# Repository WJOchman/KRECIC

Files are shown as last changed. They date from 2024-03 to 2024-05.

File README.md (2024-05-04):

# KRECIC (Knowledge and Robotics Educational Companion for Interactive Computing) | A Modular Wheeled Robot for Educational Usage
## ELEE1036 Individual Project at the University of Greenwich | Academic Year 2023/24

<p align="center">
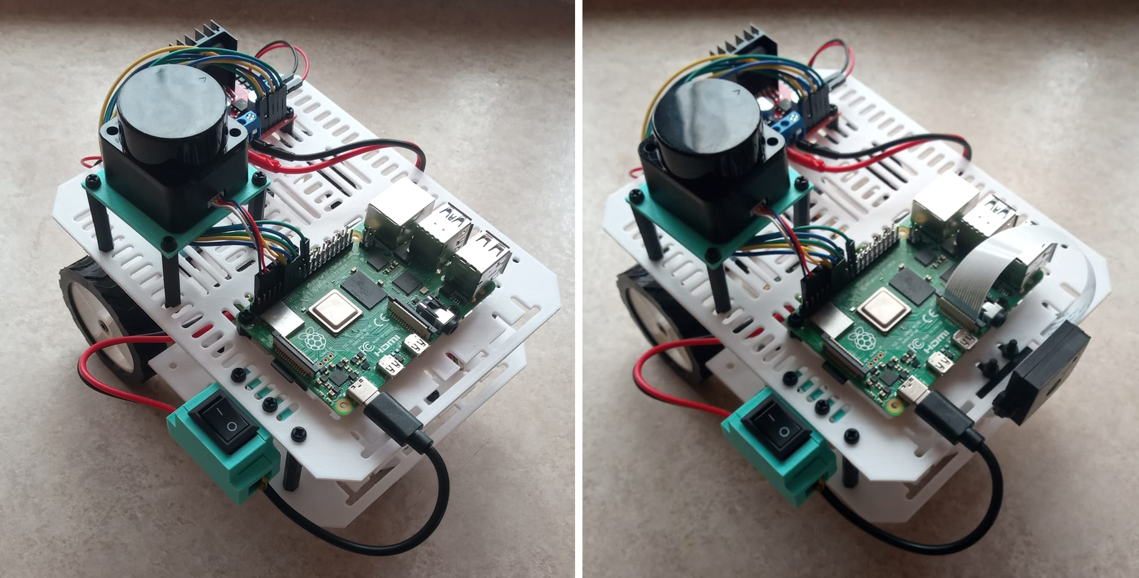
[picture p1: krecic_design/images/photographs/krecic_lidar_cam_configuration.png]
krecic_image
  
</p>

## Table of Contents
- [Introduction](#introduction)
- [Hardware Setup](#hardware-setup)
  - [Components](#components)
  - [Manufacturing](#manufacturing)
  - [Assembly](#assembly)
- [Software Setup](#software-setup)
  - [Operating System](#operating-system)
  - [Robot Operating System](#robot-operating-system)
  - [Motor and Movement Control](#motor-and-movement-control)
  - [Camera Module](#camera-module)
  - [LiDAR Module](#lidar-module)
- [Contributors](#contributors)
- [License](#license) 

## Introduction
This project has been developed as a final year project for the BEng in Computer Engineering (Hons) at the University of Greenwich (Academic Year 2023/24). 

This project can only be used for educational purposes and it cannot be used for commercial purposes. All credits must be given to the creator and the University of Greenwich. 

This document presents an overview of both the hardware and software setups to successfully re-create this project. This repository is organised into two predominant sections: (a) hardware and (b) software.

## Hardware Setup
This sections outlines the necessary steps in successfully setting up KRECIC's hardware components. 

Keep in mind, that KRECIC has been designed with modularity and evolution in mind. Therefore, the exact components are not necessary. 

### Components
Consider the [Bill of Materials (BOM)](/krecic_design/electronics/KRECIC_BOM.pdf) of all electronics you may need to get started with the building of KRECIC.

### Manufacturing 
To successfully manufacture the 3D printable components found [here](/krecic_design/stl_files/), you will require either an FDM or resin printer. The following components are recommended to be manufactured using TPU, the other components may be manufactured using PLA, ABS, or PETG:
- [Tyre](/krecic_design/stl_files/tyre.stl)
- [Camera Case Front](/krecic_design/stl_files/raspi_camera_front.stl)
- [Camera Case Back](/krecic_design/stl_files/raspi_camera_back.stl)

### Assembly
When all components are acquired, the assembly process is straight forward. However, consider using a solder and shrink tubes for appropriately connecting the power switch to the main circuit. 

## Software Setup
The next section focuses on the basic software setup of KRECIC, allowing the user to test components and consequently perform educational exercises. 

### Operating System
The operating system used for this project has been Ubuntu 22.04. Consider following instructional steps [here](https://ubuntu.com/tutorials/how-to-install-ubuntu-desktop-on-raspberry-pi-4#1-overview)

### Robot Operating System (ROS2)
KRECIC uses Robot Operating System 2 Humble Hawksbill. Please consider the following installation guide from ROS2:

[Click here for ROS2 Humble Installation Guide](https://docs.ros.org/en/humble/Installation/Ubuntu-Install-Debians.html)

### Motor and Movement Control
To test motor control please follow the circuit setup as demonstrated in the following diagrams, [click here](/krecic_design/electronics/diagrams/testing_circuits/motor_test_diagrams.pdf)

Upon successful circuit setup, start with the single motor test, then follow up with the double motor test. Lastly, you can control KRECIC using OpenSSH (as long as both KRECIC's raspberry pi, and your main machine are on the same network). [Click here](/krecic_code/motor_control/) to explore the motor control tests.

### Camera Module
To successfully mount and test the camera module, follow the following steps: 

1. Connect the camera module to the Raspberry Pi: 
    <p align="center">
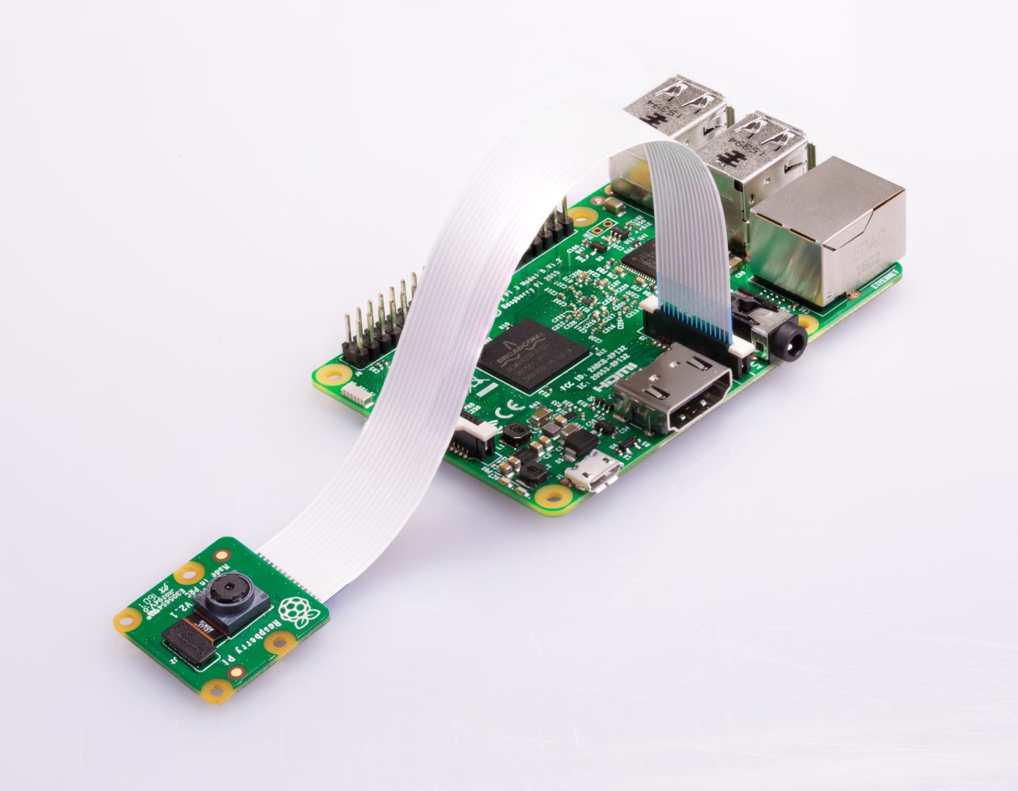
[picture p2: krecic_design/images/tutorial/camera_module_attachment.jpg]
camera_module_attachment
      
    </p>

2. Verify Camera Connection and Permissions:
    
    After connecting the camera module to the Raspberry Pi, confirm that the camera is recognised using the following:

    ```
    vcgencmd get_camera
    ```

    The output of this command should produce the following output:

    ```
    supported=1 detected=1
    ```
    
    Check if your username has access to the camera by using the following command:

    ```
    groups 
    ```

    The output of this command should `video`. If not, use the following command to add your username to the `video` group:

    ```
    sudo usermod -aG video <your_username>
    ```

3. Install `raspi-config`:

    ```
    sudo apt install raspi-config
    sudo raspi-config
    ```

4. Enable `Legacy Camera`, `SPI`, and `I2C` in Interface Options

    <p align="center">
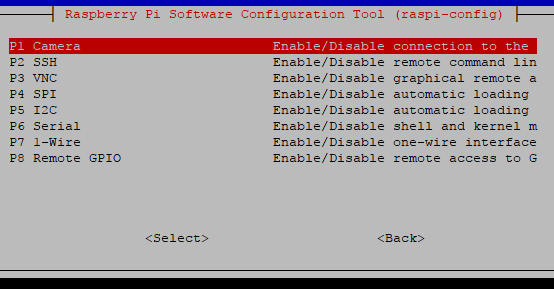
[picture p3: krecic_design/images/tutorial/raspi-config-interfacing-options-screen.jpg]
      
    </p>
  
    Restart your Raspberry Pi.  

5. Install FFMPEG

    Multiple softwares can be installed to test the functionality of the camera. The camera module can be tested with `libcamera`, `ros2`, `opencv`, etc. This tutorial uses `ffmpeg`.

    ```
    sudo apt install ffmpeg
    ```

5. Perform Picture Test

    ```
    ffmpeg -f video4linux2 -i /dev/video0 -vframes 1 test_image.jpg
    ```

6. Perform Video Recording Test

    ```
    ffmpeg -f video4linux2 -i /dev/video0 -t 10 -c:v libx264 test_video.mp4
    ```

7. Perform Live Stream Test

    ```
    ffmpeg -f video4linux2 -i /dev/video0 -f mpegts - | ffplay -
    ```

### LiDAR Module
To successfully mount and test the LD06/LD19 LiDAR module please consider the repository by ldrobotSensorTeam. This tutorial presents a 4-step process on how to mount the LiDAR sensor, and use ROS2 to test it's functionality. It is advisable that you already have ROS2 installed on your Raspberry Pi. Consider the following link:

  [LD06/LD19 Testing Instructions by ldrobotSensorTeam](https://github.com/ldrobotSensorTeam/ldlidar_stl_ros2?tab=readme-ov-file#Instructions)

## Contributors
- [@WJOchman](https://github.com/WJOchman)
- Contact:
  - [Wojciech Ochman | LinkedIn](https://www.linkedin.com/in/wojciech-j-ochman/)  

## License
<p xmlns:cc="http://creativecommons.org/ns#" >This work is licensed under <a href="http://creativecommons.org/licenses/by-nc-sa/4.0/?ref=chooser-v1" target="_blank" rel="license noopener noreferrer" style="display:inline-block;">CC BY-NC-SA 4.0</a></p>

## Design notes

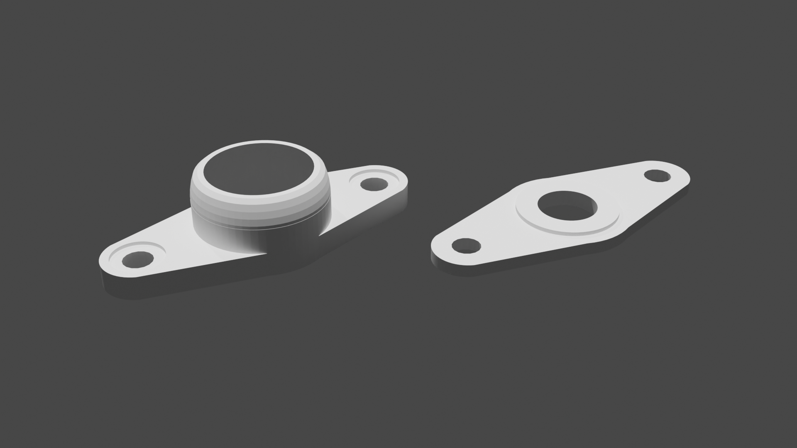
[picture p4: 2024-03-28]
krecic_design/images/renders/caster_wheel_holder_3.png

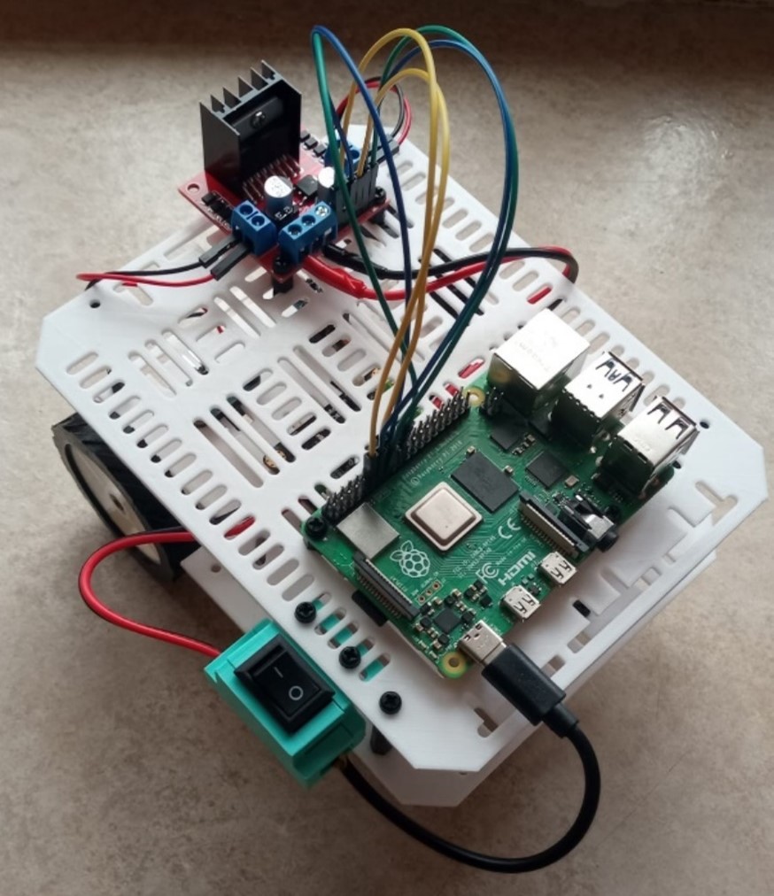
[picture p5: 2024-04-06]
krecic_design/images/photographs/krecic_main_configuration.jpg

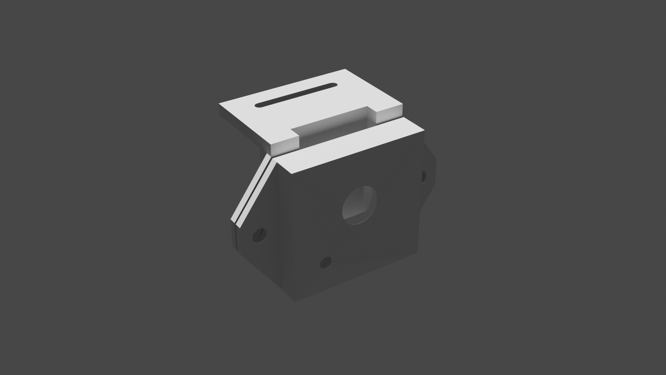
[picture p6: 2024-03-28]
krecic_design/images/renders/raspi_cam_case_1.png

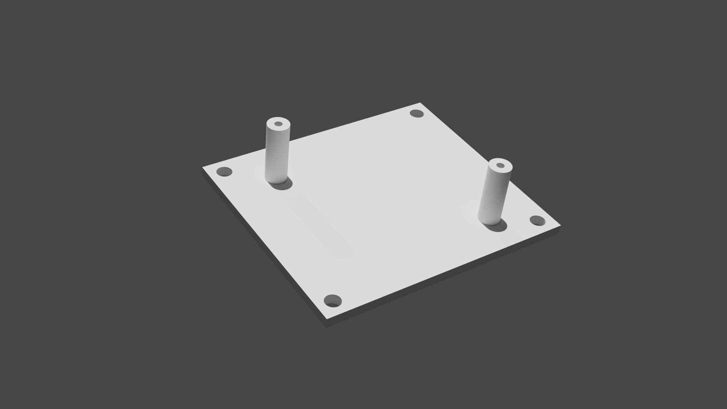
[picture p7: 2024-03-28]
krecic_design/images/renders/lidar_bracket.png

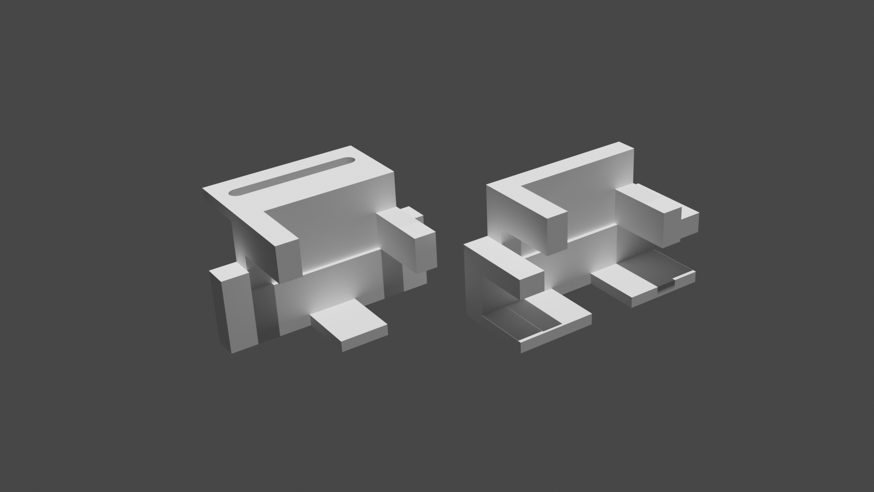
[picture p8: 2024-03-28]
krecic_design/images/renders/switch_case_1.png

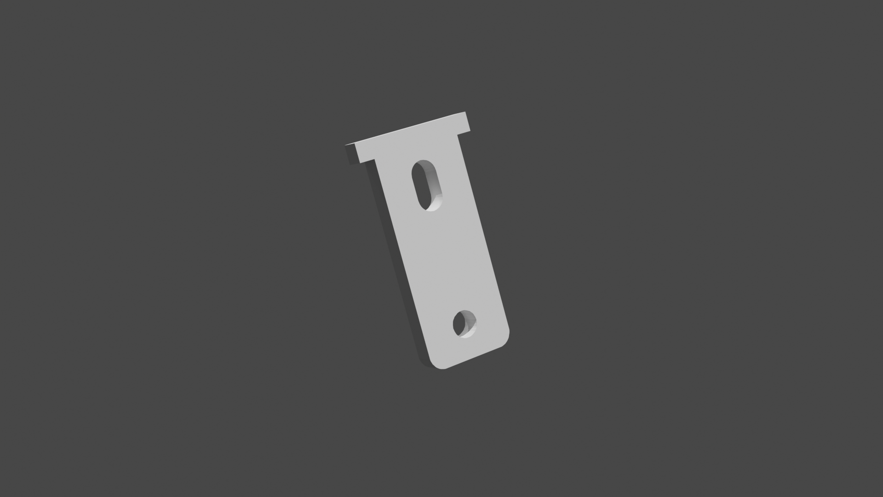
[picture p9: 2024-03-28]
krecic_design/images/renders/motor_bracket.png

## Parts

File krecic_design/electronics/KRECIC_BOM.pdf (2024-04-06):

Created by: Wojciech Jacek Ochman | University of Greenwich 2023/24

## KRECIC Bill of Materials (BOM)

Component No. | Component Name | Component Picture | Component Quantity | Component Price (£)
1 | Battery | | 1 | 17.00

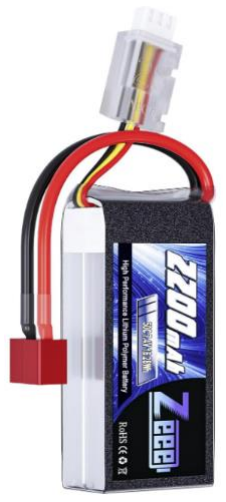
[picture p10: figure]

2 | Battery T Cable | | 1 | 1.40
3 | Camera | | 1 | 9.99
4 | Caster Ball | | 12 | 1.20
5 | Encoders + Discs | | 2 | 2.70

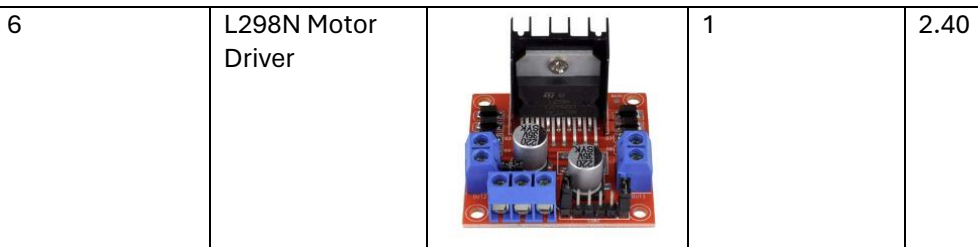
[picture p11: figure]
L298N Motor Driver
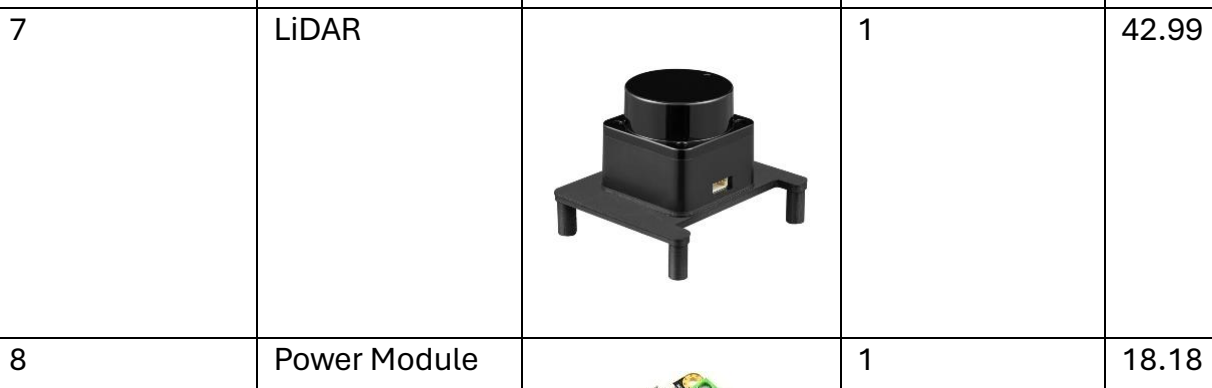
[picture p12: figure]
LiDAR; Power Module

9 | Raspberry Pi | 1 | 55.99

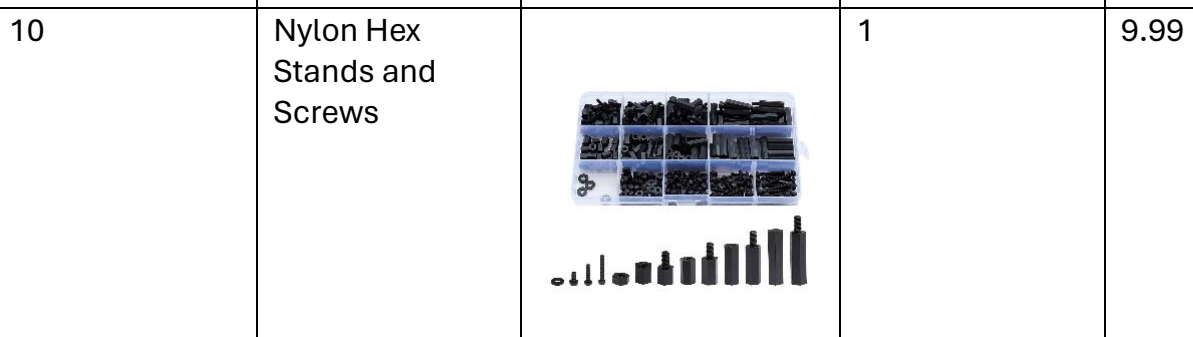
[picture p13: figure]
Nylon Hex Stands and Screws

11 | Power Switch | 1 | 0.79

12 | TCRT5000 IR Sensors | 2 | 2.33

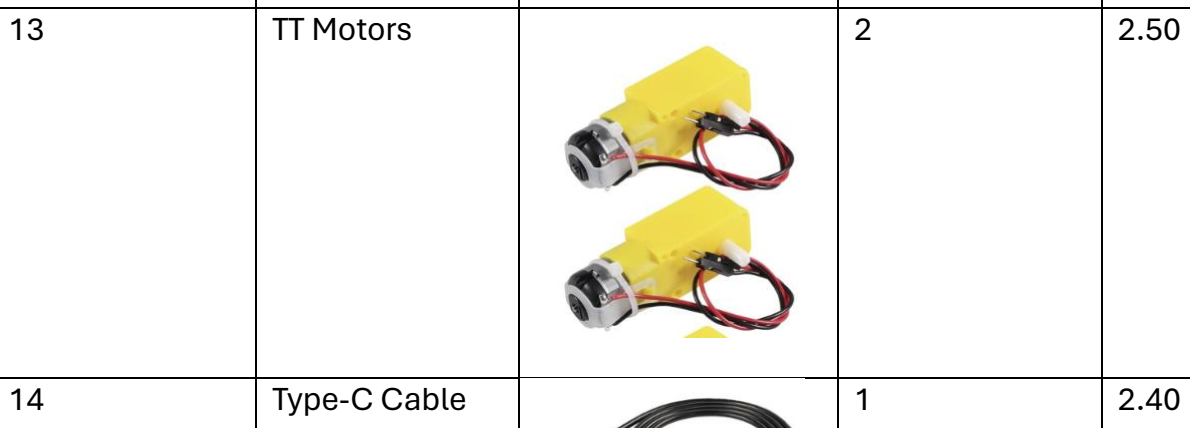
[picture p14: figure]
TT Motors; Type-C Cable

Total Component Cost | | | £169.86

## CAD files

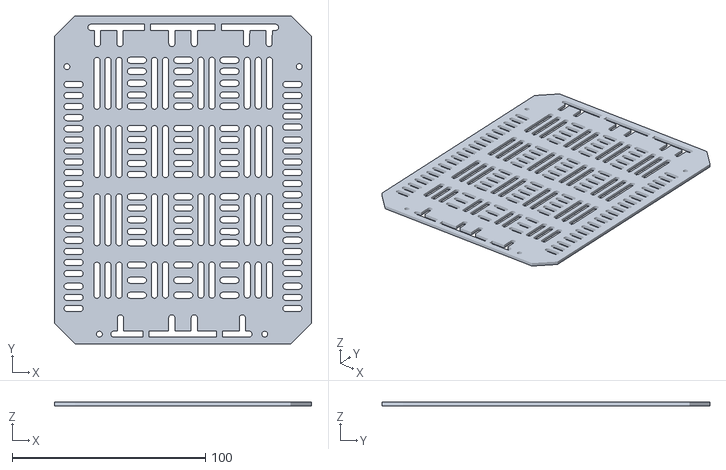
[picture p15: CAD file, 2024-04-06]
krecic_design/stl_files/upper_body.stl
133.2 x 169.8 x 2.00

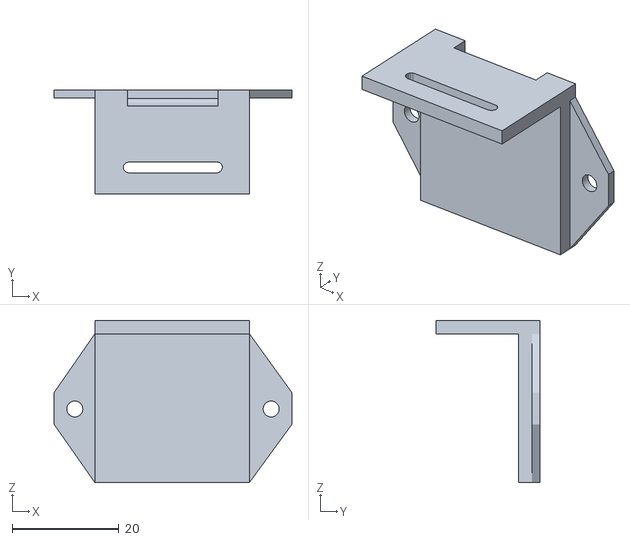
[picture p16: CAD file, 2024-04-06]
krecic_design/stl_files/raspi_camera_back.stl
44.7 x 19.5 x 30.4

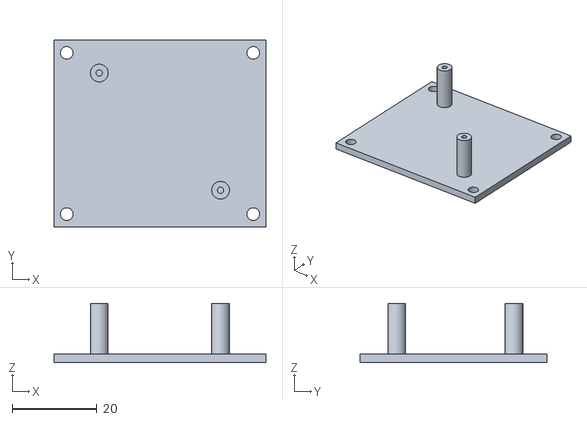
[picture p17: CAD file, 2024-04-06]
krecic_design/stl_files/lidar_stand.stl
50.0 x 44.0 x 14.0

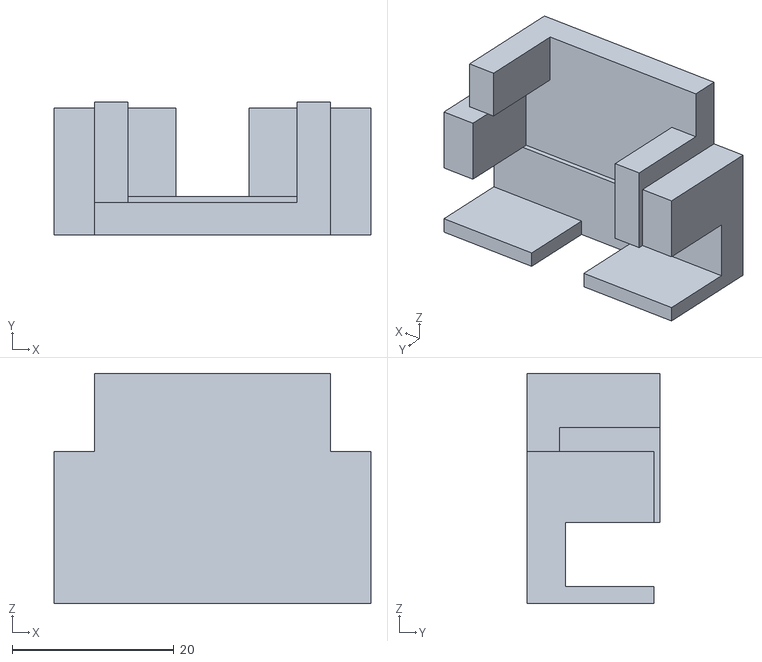
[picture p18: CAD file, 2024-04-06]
krecic_design/stl_files/switch_bracket_a.stl
39.2 x 16.5 x 28.5

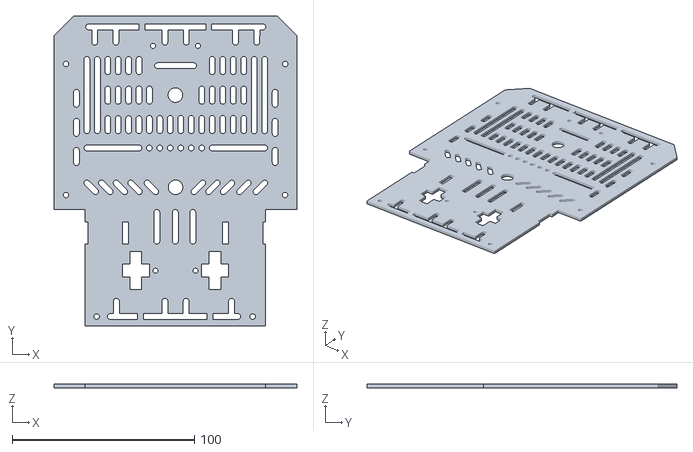
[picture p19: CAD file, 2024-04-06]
krecic_design/stl_files/lower_body.stl
133.2 x 169.8 x 2.00

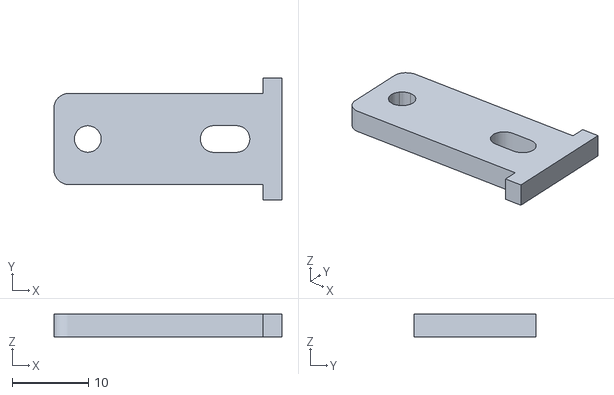
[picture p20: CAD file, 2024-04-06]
krecic_design/stl_files/motor_bracket.stl
30.0 x 16.0 x 3.00

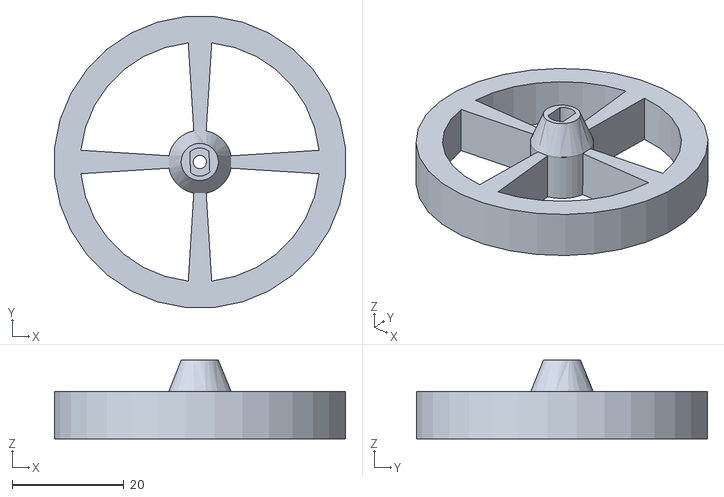
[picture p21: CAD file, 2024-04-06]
krecic_design/stl_files/rim.stl
52.2 x 52.2 x 14.1

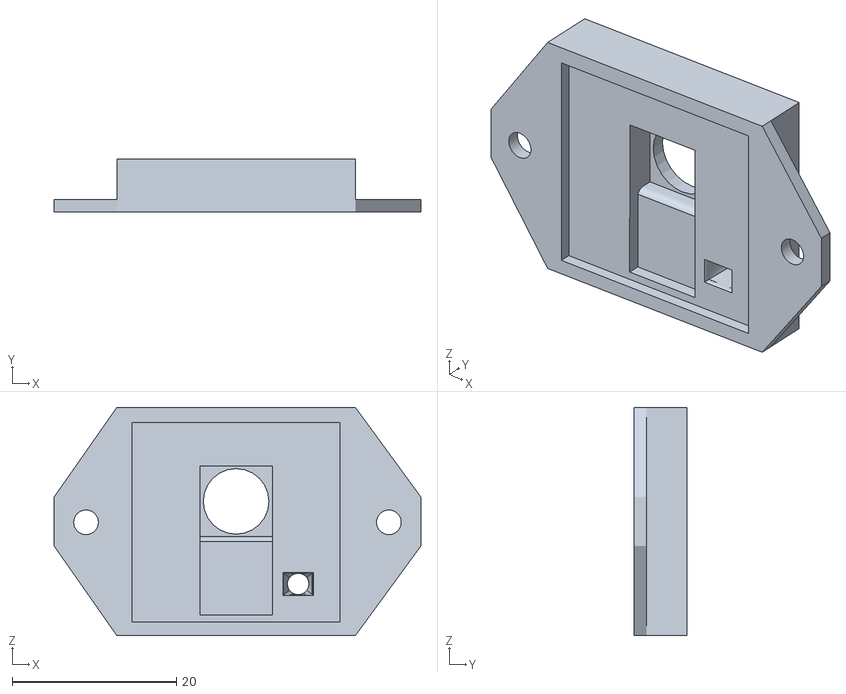
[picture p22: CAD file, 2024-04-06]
krecic_design/stl_files/raspi_camera_front.stl
44.7 x 6.41 x 27.8

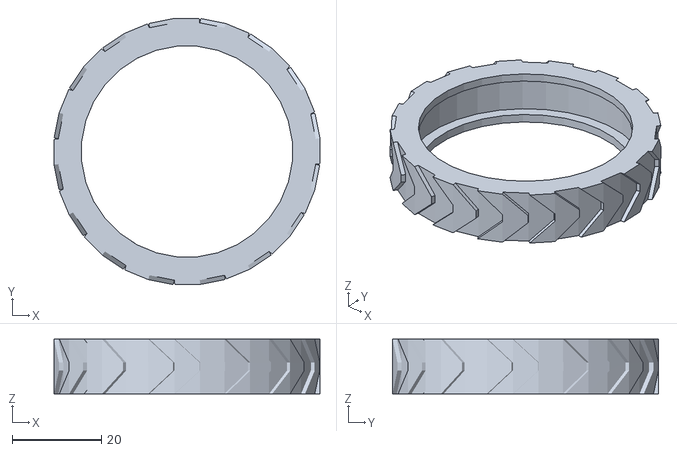
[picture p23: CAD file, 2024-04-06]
krecic_design/stl_files/tyre.stl
59.5 x 59.5 x 12.2

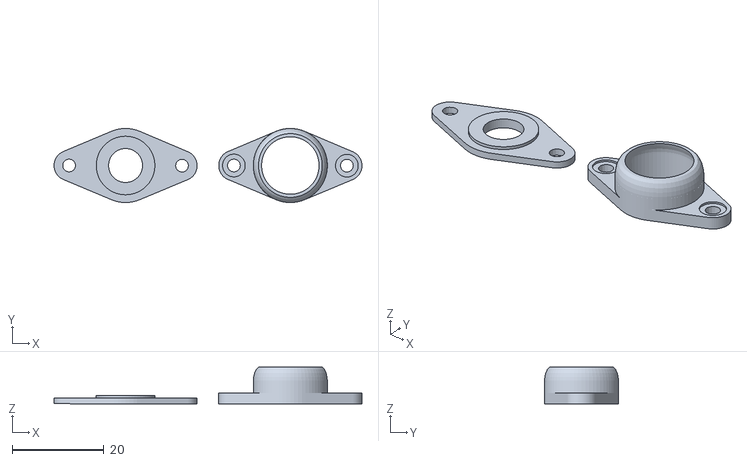
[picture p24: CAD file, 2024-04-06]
krecic_design/stl_files/caster_ball_holder.stl
67.2 x 16.2 x 8.02

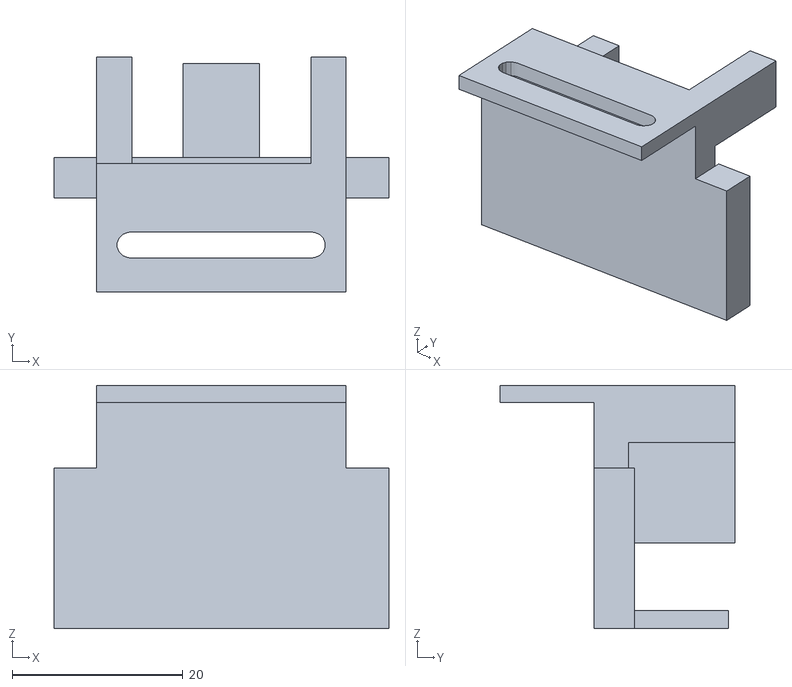
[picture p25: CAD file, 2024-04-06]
krecic_design/stl_files/switch_bracket_b.stl
39.2 x 27.5 x 28.5

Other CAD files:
krecic_design/cad_files/caster_ball_holder.blend
krecic_design/cad_files/ir_sensors_bracket.blend
krecic_design/cad_files/lidar_stand.blend
krecic_design/cad_files/lower_body.blend
krecic_design/cad_files/motor_bracket.blend
krecic_design/cad_files/raspi_camera_back.blend
krecic_design/cad_files/raspi_camera_front.blend
krecic_design/cad_files/rim.blend
krecic_design/cad_files/switch_bracket_a.blend
krecic_design/cad_files/switch_bracket_b.blend
krecic_design/cad_files/tyre.blend
krecic_design/cad_files/upper_body.blend

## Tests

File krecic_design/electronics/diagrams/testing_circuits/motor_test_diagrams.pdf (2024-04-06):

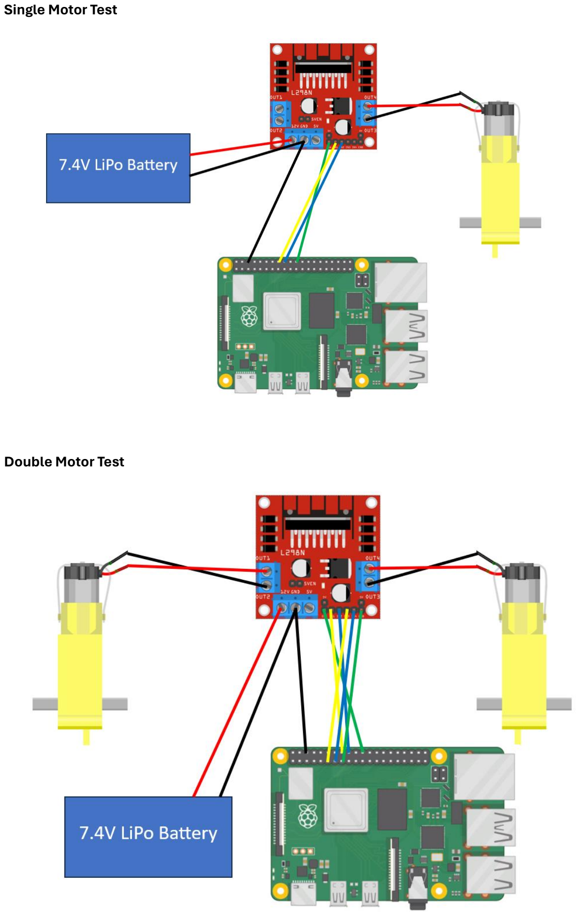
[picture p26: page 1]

Single Motor Test

Double Motor Test

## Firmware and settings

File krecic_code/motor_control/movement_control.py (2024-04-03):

import RPi.GPIO as GPIO
import time
import curses

in1 = 23
in2 = 24
en1 = 25

in3 = 17
in4 = 27
en2 = 22

GPIO.setmode(GPIO.BCM)
GPIO.setup(in1, GPIO.OUT)
GPIO.setup(in2, GPIO.OUT)
GPIO.setup(en1, GPIO.OUT)

GPIO.setup(in3, GPIO.OUT)
GPIO.setup(in4, GPIO.OUT)
GPIO.setup(en2, GPIO.OUT)

pwm_a = GPIO.PWM(en1, 1000)
pwm_b = GPIO.PWM(en2, 1000)

pwm_a.start(0)
pwm_b.start(0)

def stop_motors():
    pwm_a.ChangeDutyCycle(0)
    pwm_b.ChangeDutyCycle(0)

def forward():
    GPIO.output(in1, GPIO.HIGH)
    GPIO.output(in2, GPIO.LOW)
    GPIO.output(in3, GPIO.HIGH)
    GPIO.output(in4, GPIO.LOW)
    pwm_a.ChangeDutyCycle(75)
    pwm_b.ChangeDutyCycle(75)

def backward():
    GPIO.output(in1, GPIO.LOW)
    GPIO.output(in2, GPIO.HIGH)
    GPIO.output(in3, GPIO.LOW)
    GPIO.output(in4, GPIO.HIGH)
    pwm_a.ChangeDutyCycle(75)
    pwm_b.ChangeDutyCycle(75)

def left():
    GPIO.output(in1, GPIO.LOW)
    GPIO.output(in2, GPIO.HIGH)
    GPIO.output(in3, GPIO.HIGH)
    GPIO.output(in4, GPIO.LOW)
    pwm_a.ChangeDutyCycle(75)
    pwm_b.ChangeDutyCycle(75)

def right():
    GPIO.output(in1, GPIO.HIGH)
    GPIO.output(in2, GPIO.LOW)
    GPIO.output(in3, GPIO.LOW)
    GPIO.output(in4, GPIO.HIGH)
    pwm_a.ChangeDutyCycle(75)
    pwm_b.ChangeDutyCycle(75)

def control(stdscr):
    stdscr.nodelay(True)
    stdscr.clear()

    while True:
        char = stdscr.getch()

        if char == ord('q'):
            break
        elif char == ord('w'):
            forward()
        elif char == ord('s'):
            backward()
        elif char == ord('a'):
            left()
        elif char == ord('d'):
            right()
        else:
            stop_motors()
        
        time.sleep(0.1)

try:
    curses.wrapper(control)
finally:
    pwm_a.stop()
    pwm_b.stop()
    GPIO.cleanup()

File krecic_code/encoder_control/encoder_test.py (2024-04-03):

import RPi.GPIO as GPIO
import time

GPIO.setmode(GPIO.BCM)

in1 = 23
in2 = 24
en = 25

GPIO.setup(in1, GPIO.OUT)
GPIO.setup(in2, GPIO.OUT)
GPIO.setup(en, GPIO.OUT)

pwm = GPIO.PWM(en, 1000)
pwm.start(0)

encoder = 22
GPIO.setup(encoder, GPIO.IN, pull_up_down=GPIO.PUD_UP)
encoder_count = 0

def encoder_callback(channel):
    global encoder_count
    encoder_count += 1

GPIO.add_event_detect(encoder, GPIO.RISING, callback=encoder_callback)

def motor_forward(speed_pct):
    GPIO.output(in1, GPIO.HIGH)
    GPIO.output(in2, GPIO.LOW)
    pwm.ChangeDutyCycle(speed_pct)

try:
    motor_forward(50)
    time.sleep(5)
    motor_forward(0)
    print("Encoder Count: ", encoder_count)

except KeyboardInterrupt:
    print("Program Stopped")

finally:
    pwm.stop()
    GPIO.cleanup()

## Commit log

2024-03-28 cad_commit
    cad commit for krecik design
    [camera-case-back_V1.3.blend, camera-case-back_v1.5.blend, camera-case-front.blend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]
2024-03-28 stl_commit
    stl commit for krecik chassis design
    [camera-case-back_TEST.stl, camera-case-back_v.1.3.stl, camera-case-back_v.1.4.stl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]
2024-03-28 chassis renders
2024-03-28 test_code
    test code for motor control, remote control via ssh, and optical encoder readings
2024-03-28 test_code
    test python scripts for motor control, remote movement control over ssh, and optical encoder readings
2024-04-03 Renamed File Structure, Moved Files and Folders
    [camera-case-back_TEST.stl, camera-case-back_V1.3.blend, camera-case-back_v.1.3.stl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]
2024-04-06 KRECIC CAD Design Updates
    [camera-case-back_V1.3.blend, camera-case-back_v1.5.blend, camera-case-front.blend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]
2024-04-06 KRECIC STL Files Update
    [camera-case-back_TEST.stl, camera-case-back_v.1.3.stl, camera-case-back_v.1.4.stl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]
2024-04-06 Created Electronics Folder, Moved Datasheets, Uploaded Circuit Design Diagram
2024-04-06 Added Bill of Materials (BOM) PDF
2024-04-06 Updated README.md and Added Motor Control Circuit Diagrams
2024-05-04 Updated README file with Camera Instructions
